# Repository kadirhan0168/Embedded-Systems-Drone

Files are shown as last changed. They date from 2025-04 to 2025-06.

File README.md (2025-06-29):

# Embedded Systems Drone

## Description

This project implements a WiFi-controlled drone using ESP32 microcontroller with MPU6050 accelerometer/gyroscope for stabilization. The drone can be controlled via a web interface that displays real-time orientation data and allows adjustment of PID parameters.

**Want to understand how it works internally?**  
See the [Project Overview Document](docs/overview.md) for full system architecture, hardware schematics, software design, flowcharts, API docs, and more.

### Features

The system has the following features:

- PID control for drone stabilization
- Web-based controller dashboard
- UDP communication for emergency stop and telemetry
- Power-saving sleep mode
- Watchdog timer for system reliability

## Prerequisites

### Hardware

#### Drone:
- ESP32CAM development board
- ESP32-CAM-MB micro USB programmer
- Jumper wires
- MPU6050 6-axis accelerometer/gyroscope
- 4x 8520 brushed motors
- 4x MOSFET-based motor drivers
- 2x LiPo batteries
- WiFi network
- Drone frame STL files

#### Telemetry & Emergency Stop Controller:
- ESP32 development board
- 16x2 I2C LCD
- Button
- 10kΩ resistor

### Software

- ESP-IDF
- Arduino Core for ESP32
- Required libraries:
  - `MPU6050` (I2C communication)
  - `WiFi`
  - `ESPAsyncWebServer`
  - `WiFiUdp`

## Get Started

1. Clone this repository:
   ```bash
   git clone https://github.com/kadirhan0168/Embedded-Systems-Drone.git
   ```
2. Set up ESP-IDF development environment.
3. Add Arduino as a component to your project.
4. Configure the project:

   ```bash
   idf.py menuconfig
   ```

## Setup

### Drone:

1. Build the drone.
2. Wire all components according to `docs/schematics/embedded-systems-drone.pdf`.
3. Adjust WiFi credentials in `main/main.cpp`.
4. Connect ESP32-CAM-MB micro USB programmer to the onboard ESP32CAM module through jumper wires. Make sure to also connect IO0 to GND when flashing.
5. Set correct serial port.
6. Build and flash the project using UART.
7. Open the serial monitor to find the controller dashboard IP.

### Telemetry & Emergency Stop Controller:

1. Build the Telemetry & Emergency Stop Controller according to `docs/schematics/embedded-systems-telemetry-controller.pdf`.
2. Power the ESP32 through USB.

## Usage

The drone will initialize its system and connect to WiFi when powered on. Connect to the controller dashboard by accessing the drone's IP address (acquired from serial monitor) in a web browser. 

The power slider increases the power output of the motors. The power value is the PWM signal with 0 being the lowest and 255 being the highest power output. The directional buttons move the drone along the X- and Y-axes through roll & pitch movements. The rotation controls handle the yaw movements to rotate the drone along the Z-axis.

The PID terms can be adjusted through the controller dahsboard using the `Kp`, `Ki`, and `Kd` fields. :warning:**Attention**:warning: — The PID terms **are not** saved, they will get lost if the connection to the drone disconnects. Save the PID terms manually if they are of importance.

The Telemetry & Emergency Stop Controller will initialize its system and attempt connecting to the drone's access point when powered on. It will display the drone's pitch and roll values on the LCD when the connection has been set up. Pressing the button will trigger an interrupt cutting all power to the drone's motors immediately.

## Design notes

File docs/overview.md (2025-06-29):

# Project Overview: Embedded Systems Drone

This document provides a high-level overview of the system design and architecture for the Embedded Systems Drone project. It links to all major documentation files, including hardware schematics, software architecture, 3D designs, API documentation, and test reports.

---

## 1. Hardware Design

### 1.1 Drone Hardware

- [Drone Circuit Schematics (PDF)](schematics/embedded-systems-drone.pdf)
  
  Wiring diagram for the drone's components, including the ESP32-CAM, MPU6050 IMU, motor drivers, and power supply.

- [Drone Frame STL File (V3)](designs/V3/drone.stl)
  
  3D-printable STL models of the drone's frame designed for an X-configuration with four arms:
  - V1 was designed for use with 716 motors.
  - V2 was designed for use with 8520 motors.
  - V3 is a bigger frame whic was also designed for use with 8520 motors.

### 1.2 Telemetry & Emergency Stop Controller

- [Controller Circuit Schematics (PDF)](schematics/embedded-systems-telemetry-controller.pdf)

  Full schematic for the telemetry controller, including button wiring, I²C LCD, and UDP communication to the drone.

### 1.3 Hardware Architecture

- [System Architecture Diagram](diagrams/architecture-design-embedded-systems.png)
  
  High-level component diagram showing the hardware and subsystem layout of both the drone and the telemetry controller. Arrows represent interaction and data flow between physical components and modules.

---

## 2. Software Design

### 2.1 Software Architecture
- [Data Flow Diagram](diagrams/dataflow-embedded-systems.png)

  Diagram outlining how data moves between components in the system, such as I²C, UDP, PWM.

### 2.2 Flowcharts

- [Drone Flowchart](diagrams/flowchart-drone-embedded-systems.png)

  Step-by-step control logic of the drone’s firmware, including tasks like PID control, WiFi, telemetry broadcast, UDP listener.

- [Telemetry Controller Flowchart](diagrams/flowchart-telemetry-embedded-systems.png)

  Logical flow of the telemetry controller from setup to emergency stop trigger and telemetry display.

### 2.3 HTTP API

- [HTTP Endpoint Documentation](HTTP/HTTP_API.md)

  Full list and explanation of HTTP endpoints exposed by the drone’s web server, including `/setMotorPower`, `/getMPUData`, and `/setPID`.

---

## 3. Test Reports

- [Test Reports](test-reports/drone-test-reports.md)

  Results from testing the drone's core features.

---

## Related Code Files

| Module | Location |
|---|---|
| Drone Firmware | `firmware/drone/main/main.cpp` |
| Telemetry Controller Code | `firmware/telemetry_controller/drone_telemetry_controller.ino` |

---

## 🔗 Quick Links

- [Project README](../README.md)
- [Setup Instructions](../README.md#get-started)

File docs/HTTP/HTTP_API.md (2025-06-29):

# Drone Web Server API Endpoints

## General Control

| Endpoint | Method | Parameters | Description | Example Response (JSON) |
|---|---|---|---|---|
| `/setMotorPower` | GET | `value` (0–255) | Sets the motor power. Wakes up drone if sleeping. | `{"status":"OK","pitch":1.2,"roll":-0.5}` |
| `/getMPUData` | GET | — | Returns current pitch and roll values. | `{"pitch":0.0,"roll":1.8}` |
| `/getSleepStatus`| GET | — | Returns whether the drone is currently sleeping. | `{"isSleeping":false}` |

---

## Movement Commands

| Endpoint | Method | Parameters | Description | Response |
|---|---|---|---|---|
| `/moveForward`  | GET | — | Move drone forward | `"Moving Up"` |
| `/moveBackward` | GET | — | Move drone backward | `"Moving Down"` |
| `/moveLeft` | GET | — | Move drone to the left | `"Moving Left"` |
| `/moveRight` | GET | — | Move drone to the right | `"Moving Right"` |
| `/rotateLeft` | GET | — | Rotate drone counter-clockwise | `"Rotating Left"` |
| `/rotateRight`  | GET | — | Rotate drone clockwise | `"Rotating Right"` |
| `/stop` | GET | — | Stops all directional movement | `"Stopping Movement"` |

---

## PID Tuning

| Endpoint | Method | Parameters | Description | Example Response |
|---|---|---|---|---|
| `/setPID` | GET | `Kp`, `Ki`, `Kd` (floats) | Updates the PID controller constants| `"PID Updated: Kp=2.0 Ki=0.01 Kd=0.5"` |

| Endpoint  | Method | Parameters (floats)  | Description | Defaults | Example Response |
|---|---|---|---|---|---|
| `/setPID` | GET | `Kp`, `Ki`, `Kd` | Updates the PID controller constants | `Kp=1.5` | `"PID Updated: Kp=2.0 Ki=0.01 Kd=0.5"` |
| | | | | `Ki=0.003` | |
| | | | | `Kd=0.0` | |

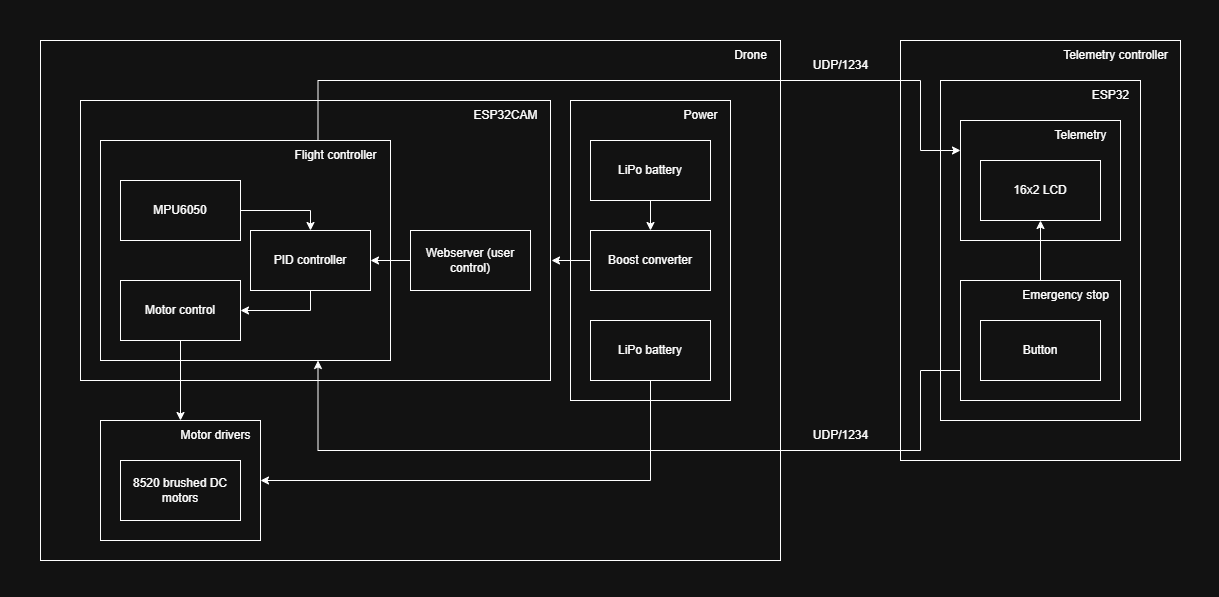
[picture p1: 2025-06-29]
docs/diagrams/architecture-design-embedded-systems.png

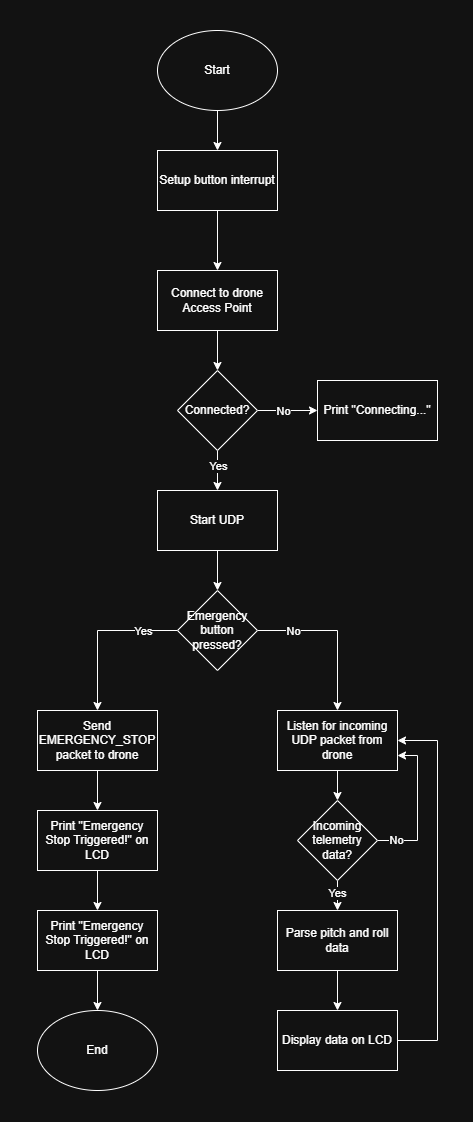
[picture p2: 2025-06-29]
docs/diagrams/flowchart-telemetry-embedded-systems.png

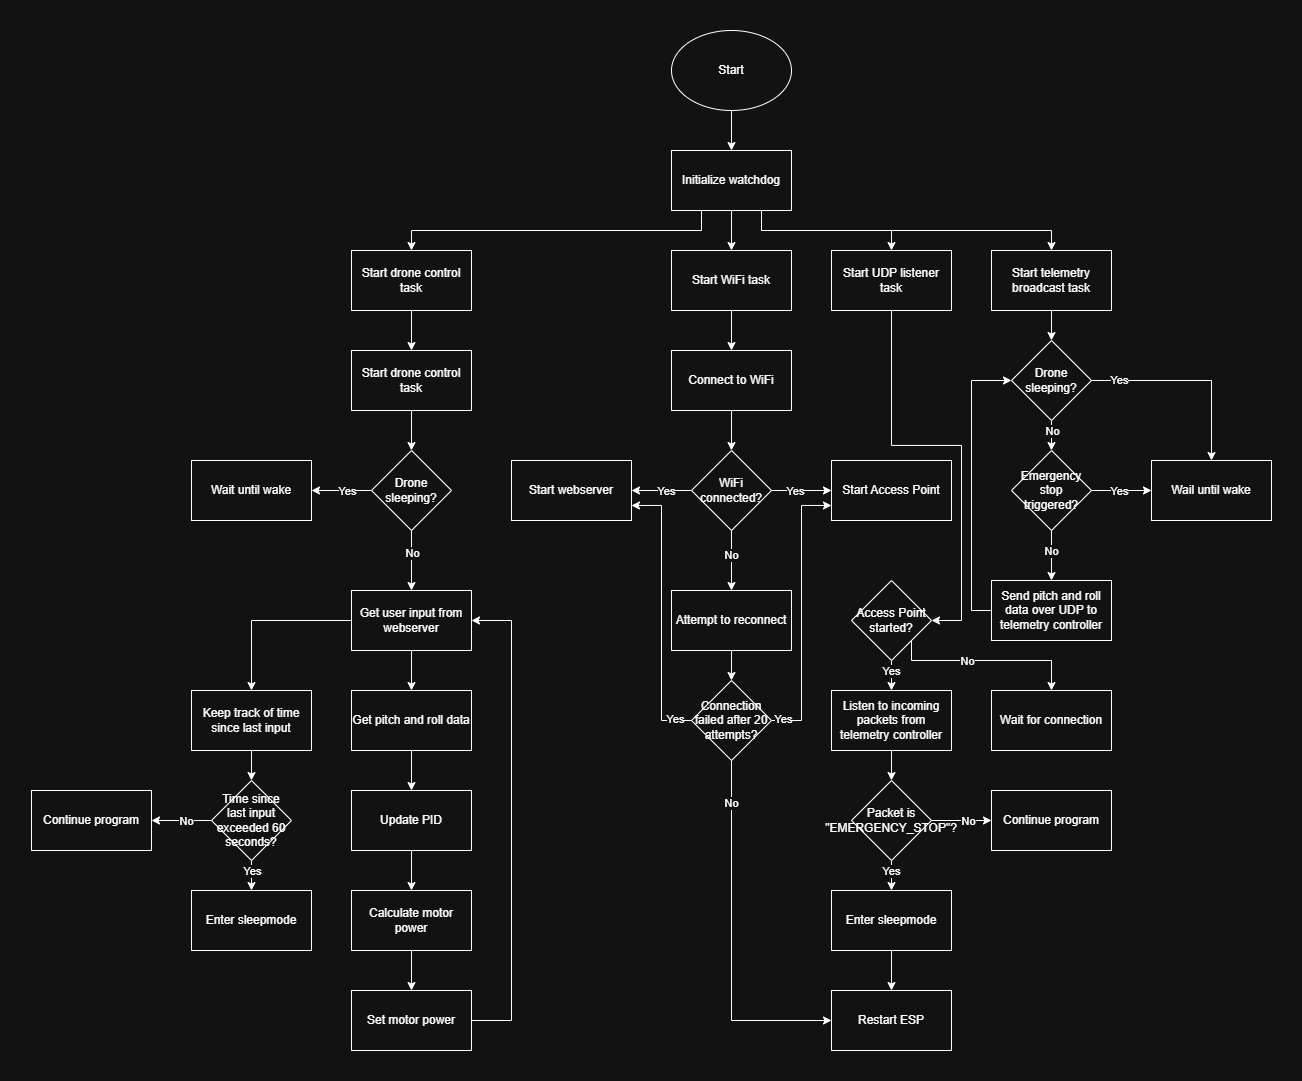
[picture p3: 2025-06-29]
docs/diagrams/flowchart-drone-embedded-systems.png

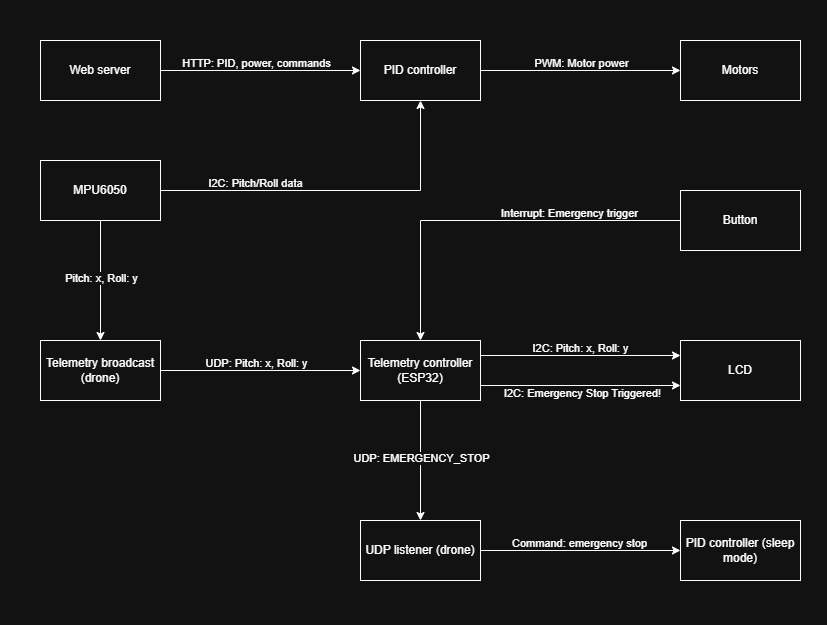
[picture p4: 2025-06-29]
docs/diagrams/dataflow-embedded-systems.png

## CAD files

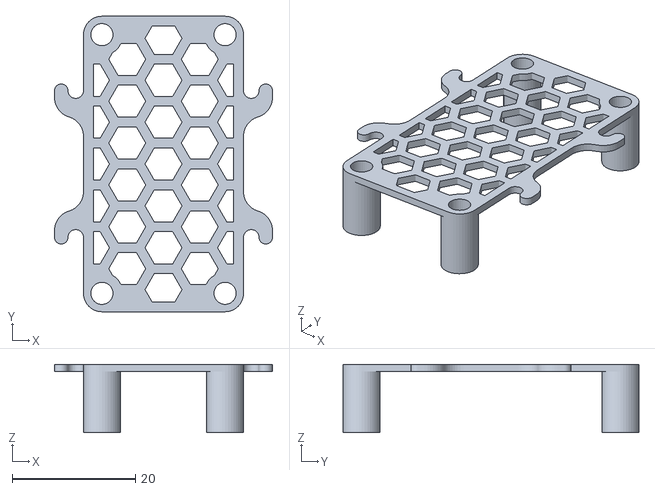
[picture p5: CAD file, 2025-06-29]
docs/designs/V3/Batteryholder.stl
35.4 x 48.0 x 11.1

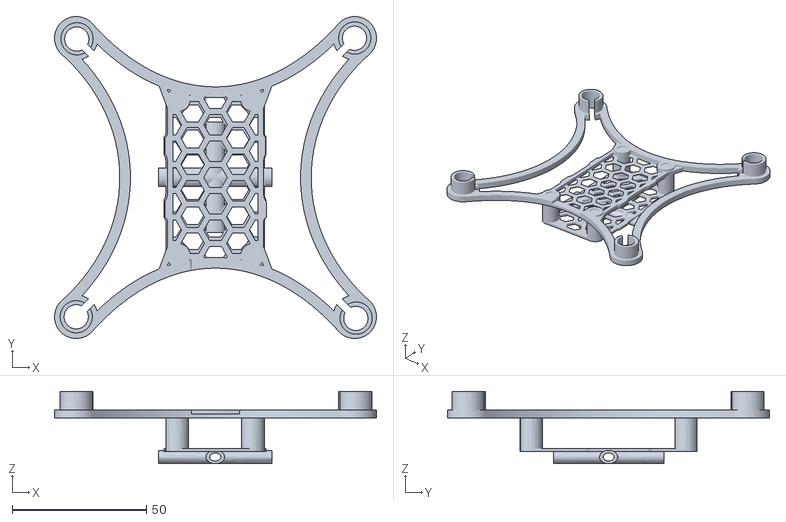
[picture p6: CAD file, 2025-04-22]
docs/designs/V3/Drone.stl
120.0 x 120.0 x 27.0

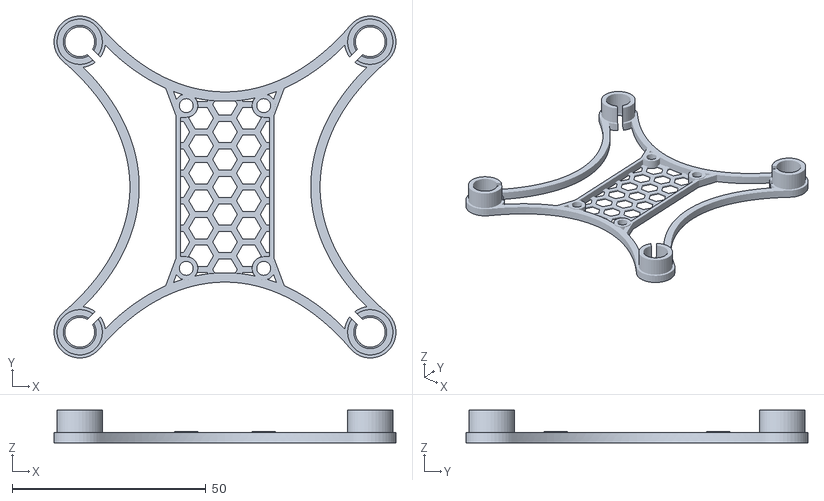
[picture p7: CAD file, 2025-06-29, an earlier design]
docs/designs/V2/micro105-bottom-v2.stl
88.3 x 88.3 x 8.50

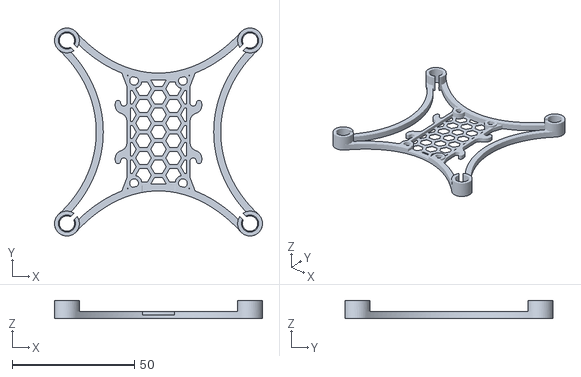
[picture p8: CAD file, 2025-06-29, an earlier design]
docs/designs/V1/micro105-bottom-v4-7mm-bottom-battery.stl
85.2 x 85.2 x 7.50

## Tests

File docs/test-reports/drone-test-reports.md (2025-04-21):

# Test report - ESP32 drone functionalities

## Test 1: Hosting webserver as controller dashboard

### Context

This test verifies that the ESP32CAM module is able to connect to WiFi and host a webserver. The webserver contains the HTML for the controller dashboard.

### Requirement

Hosting webserver for controls.

### Acceptance criteria

The ESP32CAM connects to WiFi and hosts the webserver correctly.

### Materials needed

- ESP32CAM
- ESP32-CAM-MB micro USB programmer
- WiFi network
- main.cpp

### Preparation

1. Clone the repository.
2. Connect the ESP32-CAM-MB micro USB programmer to the ESP32CAM module.
3. Select the correct serial port.
4. Build and flash main.cpp.

### Execution

1. Open serial monitor and wait for the IP address to be printed.
2. Connect to the IP address through the browser.

### Results

The browser connected to the webserver and the correct HTML page was being hosted.

### Conclusion

The test passed. The ESP32CAM module was able to connect to WiFi and host the webserver.

----

## Test 2: Throttle

### Context

This test verifies that the drone is able to increase and decrease thrust to all motors using the controller dashboard.

### Requirement  

Ascend
Descend

### Acceptance criteria

Changing the PWM signal using the controllers dashboard's slider should increase or decrease motor power output accordingly.

### Materials needed 

- Fully built drone
- Jumper wires
- ESP32-CAM-MB micro USB programmer
- WiFi network
- main.cpp
- 2x LiPo batteries

### Preparation

1. Clone the repository.
2. Connect the ESP32-CAM-MB micro USB programmer to the ESP32CAM module.
3. Change the WiFi credentials in main.cpp
4. Select the correct serial port.
5. Build and flash main.cpp.
6. Connect LiPo batteries to the drone.

### Execution

1. Open serial monitor and wait for the IP address to be printed.
2. Connect to the IP address through the browser.
3. Adjust the throttle using the slider.
4. Observe whether the drone's motors spin faster as the throttle increases, and slower as it decreases.

### Results

The drone's motors spin faster as the throttle increases. The motors spin slower when the throttle decreases and come to a full stop at a PWM signal of 0.

### Conclusion

The test passed. The motors responded accordingly to the throttle inputs.

----

## Test 3: Pitch & roll in all directions

### Context

This test verifies the movement of the drone along the X- and Y-axes.

### Requirement  

Pitch in four directions.

### Acceptance criteria

The test passes if the drone is able to pitch forward, backward, and roll to the sides to move in all four directions. It also tests wether the motors are configured correctly.

### Materials needed 

- Fully built drone
- Jumper wires
- ESP32-CAM-MB micro USB programmer
- WiFi network
- main.cpp
- 2x LiPo batteries

### Preparation

1. Clone the repository.
2. Connect the ESP32-CAM-MB micro USB programmer to the ESP32CAM module.
3. Change the WiFi credentials in main.cpp
4. Select the correct serial port.
5. Build and flash main.cpp.
6. Connect LiPo batteries to the drone.

### Execution

1. Open serial monitor and wait for the IP address to be printed.
2. Connect to the IP address through the browser.
3. Increase the throttle using the slider while holding the drone at a level where you can feel it starting to lift.
4. Press each of the four directional buttons individually and feel which way the drone wants to move.

### Results

Pressing the directional buttons made the drone want to move in the correct direction. The thrust was high enough to see the drone pulling into each direction.

### Conclusion

The test passed. The drone is able to pitch and roll accordingly based on user inputs. This also verifies that the motors are configured correctly.

----

## Test 4: Yaw left and right

### Context

This test verifies the rotational movement of the drone along the Z-axis (yaw).

### Requirement  

Yaw left and right.

### Acceptance criteria

The test passes if the drone is able to rotate clockwise and counterclockwise when the respective yaw buttons are pressed.

### Materials needed 

- Fully built drone
- Jumper wires
- ESP32-CAM-MB micro USB programmer
- WiFi network
- main.cpp
- 2x LiPo batteries

### Preparation

1. Clone the repository.
2. Connect the ESP32-CAM-MB micro USB programmer to the ESP32CAM module.
3. Change the WiFi credentials in main.cpp
4. Select the correct serial port.
5. Build and flash main.cpp.
6. Connect LiPo batteries to the drone.

### Execution

1. Open serial monitor and wait for the IP address to be printed.
2. Connect to the IP address through the browser.
3. Increase the throttle using the slider while holding the drone at a level where you can feel it starting to lift.
4. Press each of the two yaw buttons individually and feel which way the drone wants to move.

### Results

Pressing the yaw buttons made the drone want to move in the correct direction.

### Conclusion

The test passed. The drone is able to rotate along the Z-axis in both directions.

## Test 5: Reading the MPU6050 sensor via I2C

### Context
This test verifies whether the ESP32CAM can read data from the MPU6050 sensor via I2C communication.

### Requirement
The ESP32CAM must be able to read data from a connected MPU6050 sensor via I2C.

### Acceptance criteria
The sensor must return correct acceleration and gyroscopic data.

### Materials needed
- ESP32CAM
- ESP32-CAM-MB micro USB programmer
- MPU6050
- Jumper wires
- main.cpp

### Preparation
1. Connect the MPU6050 to the ESP32CAM module using jumper wires.
2. Select the correct serial port.
3. Build and flash main.cpp.

### Execution

1. Open the serial monitor.
2. Move the MPU6050 around and check whether the incoming data is correct and reliable. The stream of data should be stable and uninterrupted.

### Conclusion
The test passed. The MPU6050 readout works as expected. The data is reliable, and communication is stable. The test passed successfully.

----

## Test 6: Balance drone using MPU6050

### Context

This test verifies the balancing of the drone using the MPU6050 module and PID controller.

### Requirement  

Balance drone using gyroscope.

### Acceptance criteria

The test passes if the drone is able to ascend, maintain altitude and balance itself without drifting away more than 10 centimeters from it's initial position during 30 seconds of flight.

### Materials needed 

- Fully built drone
- Jumper wires
- ESP32-CAM-MB micro USB programmer
- WiFi network
- main.cpp
- 2x LiPo batteries
- Duct tape
- Stopwatch

### Preparation

1. Clone the repository.
2. Connect the ESP32-CAM-MB micro USB programmer to the ESP32CAM module.
3. Change the WiFi credentials in main.cpp
4. Select the correct serial port.
5. Build and flash main.cpp.
6. Connect LiPo batteries to the drone.
7. Stick a piece of duct tape to the floor and place the drone on top of it.

### Execution

1. Open serial monitor and wait for the IP address to be printed.
2. Connect to the IP address through the browser.
3. Increase the throttle using the slider until the drone starts ascending and is approximately 50 centimeters above the floor.
4. Start the stopwatch and observer the drone.

### Results

The drone struggles to maintain balance and altitude. It loses balance and crashes shortly after ascending.

### Conclusion

The test failed. The drone tries to stabilize too aggressively is not able to maintain flight. The PID controller needs further calibration.

----

## Test 7: Watchdog timer

### Context
This test verifies whether the watchdog timer in the ESP32 microcontroller functions correctly by detecting system faults and restarting the drone.

### Requirement
The ESP32 must use a watchdog timer that automatically restarts the system in case of errors.

### Acceptance criteria
The watchdog must restart the drone within 3 seconds after detecting a system error or freeze.

### Materials needed
- Fully built drone
- ESP32-CAM-MB micro USB programmer
- Jumper wires
- main.cpp

### Execution
1. Open the serial monitor.
2. Observe whether the watchdog timer gets triggered.

### Results
The watchdog timer functioned correctly. The drone restarted within the expected time after detecting a system error. No communication issues were observed during the test.

### Conclusion
The watchdog timer test was successful. The function works as required and restarts the drone within the specified time.

----

## Test 8: Sleep mode

### Context
This test checks the functionality of the sleep mode on the ESP32, which helps save energy during inactivity.

### Requirement
The ESP32 must automatically enter sleep mode during inactivity to conserve energy.

### Acceptance criteria
The drone must enter sleep mode within a minute of inactivity and correctly wake up upon receiving an input signal.

### Materials needed
- Fully built drone
- ESP32-CAM-MB micro USB programmer
- Jumper wires
- main.cpp
- WiFi network
- Stopwatch

### Execution
1. Open serial monitor and wait for the IP address to be printed.
2. Connect to the IP address through the browser.
3. Start the stopwatch and wait for the drone to go into sleep mode.

### Results
The sleep mode functioned as expected. The drone entered sleep mode after a minute of inactivity and was reactivated immediately after a trigger. A message was displayed on the controller dashboard to notify the user that the drone was in sleep mode. The MPU6050 was also powered off during this state.

### Conclusion
Sleep mode is effective, and the drone wakes correctly upon receiving input. The test passed successfully.

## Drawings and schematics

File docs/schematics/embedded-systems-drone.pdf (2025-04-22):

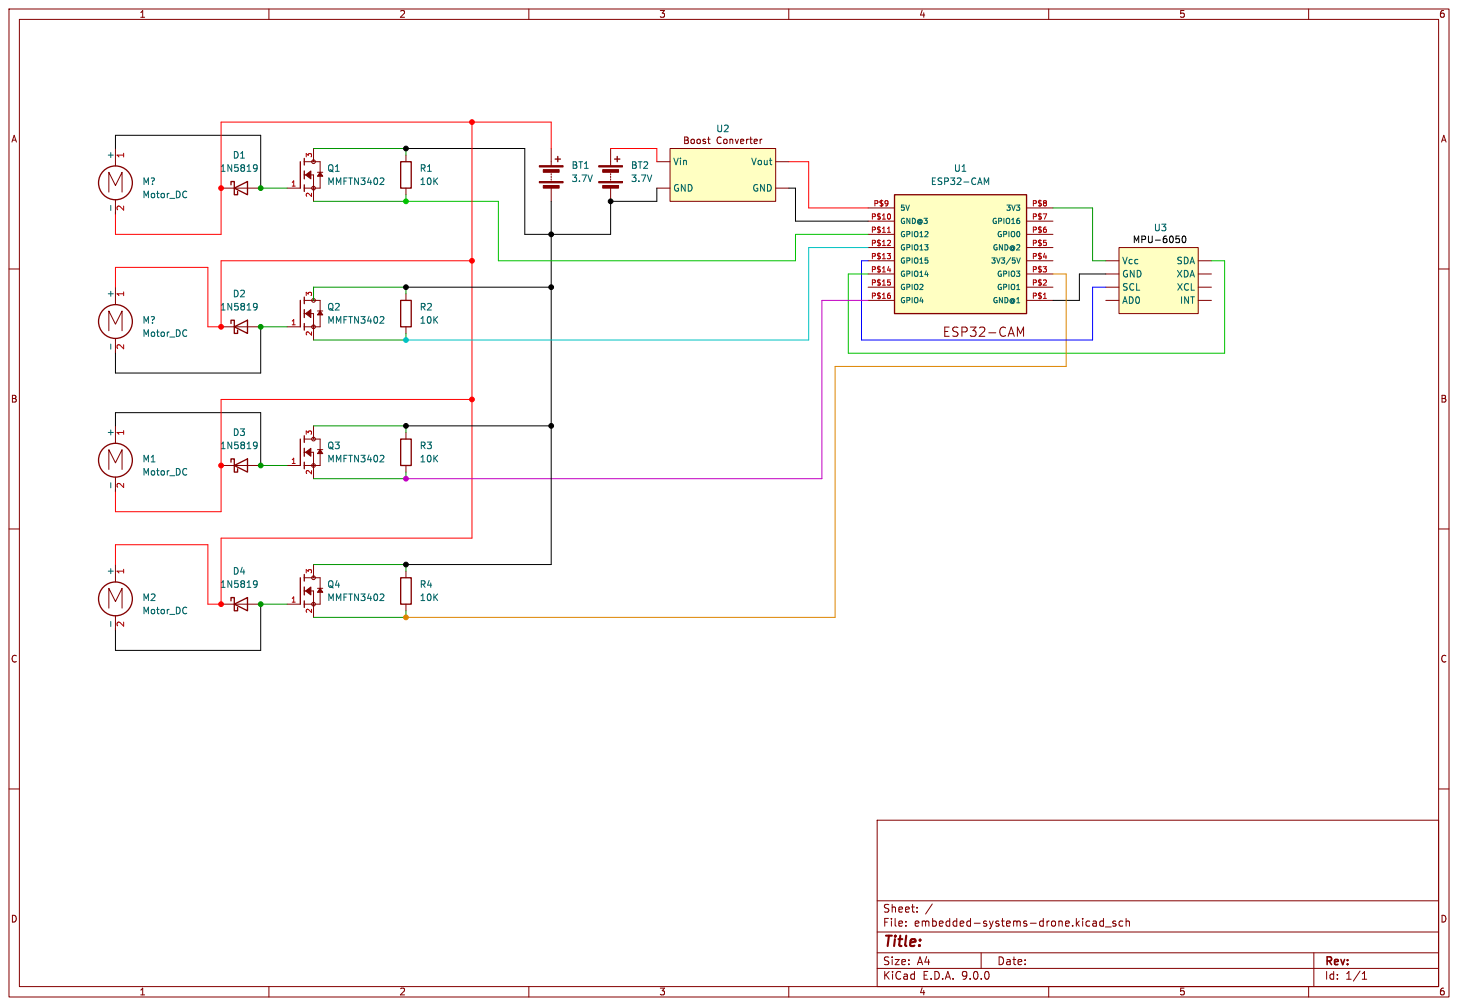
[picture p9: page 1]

Boost Converter Vin GND

Id: 1/1 Title: File: embedded-systems-drone.kicad_sch Sheet: /

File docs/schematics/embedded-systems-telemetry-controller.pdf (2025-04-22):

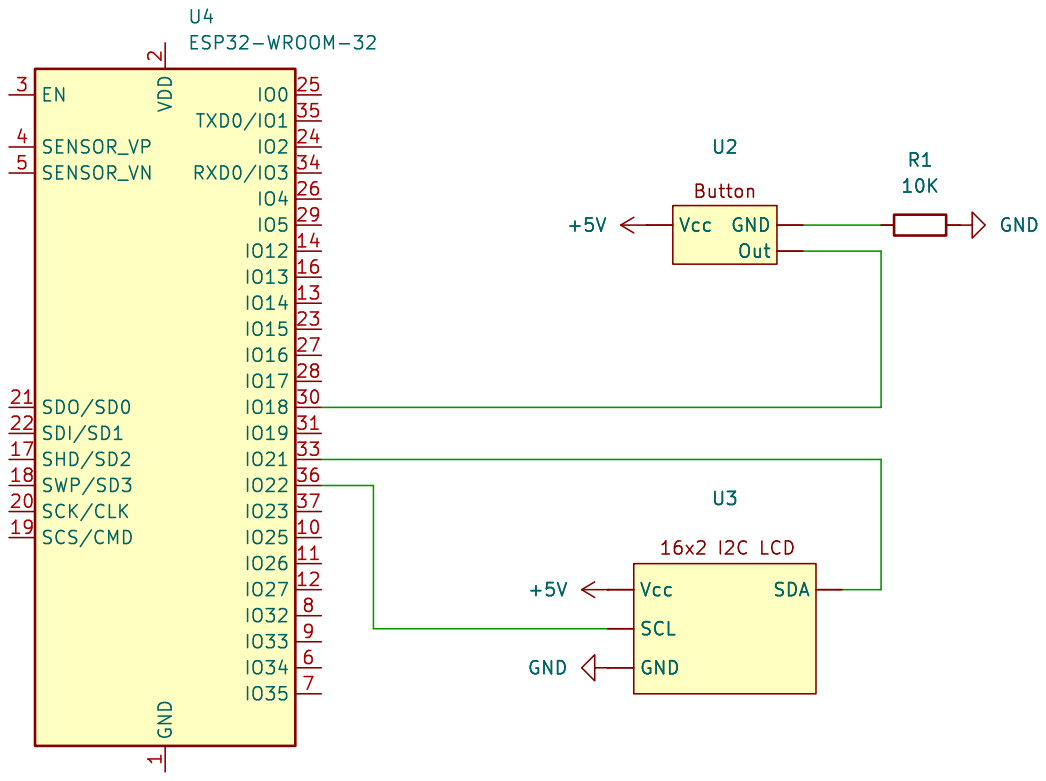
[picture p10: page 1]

Id: 1/1 Title: File: embedded-systems-telemetry-controller.kicad_sch Sheet: /

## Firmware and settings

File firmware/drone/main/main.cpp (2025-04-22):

#include <stdio.h>
#include <string.h>
#include "esp_system.h"
#include "esp_log.h"
#include "nvs_flash.h"
#include "freertos/FreeRTOS.h"
#include "freertos/task.h"
#include "mpu6050.h"
#include <driver/i2c.h>
#include "driver/ledc.h"
#include <math.h>
#include <Arduino.h>
#include <WiFi.h>
#include <ESPAsyncWebServer.h>
#include <WiFiUdp.h>
#include "esp_task_wdt.h"

#define SSID "ssid"
#define PASSWORD "password"

AsyncWebServer server(80);

#define M_PI 3.14159265358979323846

#define PIN_SDA 14
#define PIN_CLK 15
#define I2C_ADDRESS 0x68

#define MPU6050_ACCEL_XOUT_H 0x3B
#define MPU6050_PWR_MGMT_1   0x6B

#undef ESP_ERROR_CHECK
#define ESP_ERROR_CHECK(x)   do { esp_err_t rc = (x); if (rc != ESP_OK) { ESP_LOGE("err", "esp_err_t = %d", rc); assert(0 && #x);} } while(0);

// PWM definitions
#define LEDC_TIMER LEDC_TIMER_0
#define LEDC_MODE LEDC_LOW_SPEED_MODE
#define LEDC_DUTY_RES LEDC_TIMER_8_BIT
#define LEDC_FREQUENCY 4000

// MPU6050 definitions
#define I2C_MASTER_NUM I2C_NUM_0
#define I2C_MASTER_FREQ_HZ 100000
#define I2C_MASTER_SDA_IO 14
#define I2C_MASTER_SCL_IO 15
#define MPU6050_ADDR 0x68

// Motor pins
int motorPin[4] = {
    4, 
    3, 
    13, 
    12
};

// UDP configuration
WiFiUDP udp;
const unsigned int localPort = 1234;
const unsigned int remotePort = 1234;
IPAddress broadcastIP(192, 168, 4, 255);
TaskHandle_t udpTaskHandle = NULL;

// Emergency stop variables
volatile bool emergency_stop = false;
portMUX_TYPE emergency_mux = portMUX_INITIALIZER_UNLOCKED;

// Pet every 500ms
const int WDT_TIMEOUT_SEC = 5;
const int PET_INTERVAL_MS = 500;

static char mpuTag[] = "mpu6050";
static char droneTag[] = "droneControl";
static char emergencyTag[] = "emergencyController";

float pitch = 0.0;
float roll = 0.0;
float targetPitch = 0.0;
float targetRoll = 0.0;

float Kp = 1.5;
float Ki = 0.003; 
float Kd = 0.0;

float pitchError = 0.0;
float rollError = 0.0;
float pitchIntegral = 0.0;
float rollIntegral = 0.0;
float previousPitchError = 0.0;
float previousRollError = 0.0;
float pitchCorrection = 0.0;
float rollCorrection = 0.0;

int motorPower = 0;

bool isSleeping = false;
uint64_t lastActivityTime = 0;
const uint64_t sleepTimeout = 60000;

// I2C initialization
static esp_err_t i2c_master_init(void) {
    i2c_config_t conf;
    conf.mode = I2C_MODE_MASTER;
    conf.sda_io_num = I2C_MASTER_SDA_IO;
    conf.scl_io_num = I2C_MASTER_SCL_IO;
    conf.sda_pullup_en = GPIO_PULLUP_ENABLE;
    conf.scl_pullup_en = GPIO_PULLUP_ENABLE;
    conf.master.clk_speed = I2C_MASTER_FREQ_HZ;

    esp_err_t err = i2c_param_config(I2C_MASTER_NUM, &conf);
    if (err != ESP_OK) {
        return err;
    }

    return i2c_driver_install(I2C_MASTER_NUM, conf.mode, 0, 0, 0);
}

// MPU6050 initialization
void setupMPU() {
    esp_err_t ret = i2c_master_init();
    if (ret != ESP_OK) {
        ESP_LOGE(mpuTag, "I2C initialization failed: %s", esp_err_to_name(ret));
        return;
    }

    // Wake up MPU6050
    uint8_t data[2] = {0x6B, 0x00}; // PWR_MGMT_1 register
    ret = i2c_master_write_to_device(I2C_MASTER_NUM, MPU6050_ADDR, data, sizeof(data), pdMS_TO_TICKS(1000));
    
    if (ret == ESP_OK) {
        ESP_LOGI(mpuTag, "MPU6050 connected and initialized");
    } else {
        ESP_LOGE(mpuTag, "MPU6050 connection failed: %s", esp_err_to_name(ret));
        esp_restart();
    }
}

// Read MPU6050 data
void readMPU() {
    uint8_t accel_data[6];
    uint8_t gyro_data[6];
    
    // Read accelerometer data
    uint8_t reg_addr = 0x3B; // ACCEL_XOUT_H register
    esp_err_t ret = i2c_master_write_read_device(I2C_MASTER_NUM, MPU6050_ADDR, 
                                               &reg_addr, 1, accel_data, 6, pdMS_TO_TICKS(1000));
    
    if (ret != ESP_OK) {
        ESP_LOGE(mpuTag, "Failed to read accelerometer data: %s", esp_err_to_name(ret));
        return;
    }
    
    if (ret != ESP_OK) {
        ESP_LOGE(mpuTag, "Failed to read gyroscope data: %s", esp_err_to_name(ret));
        return;
    }
    
    int16_t ax = (accel_data[0] << 8) | accel_data[1];
    int16_t ay = (accel_data[2] << 8) | accel_data[3];
    int16_t az = (accel_data[4] << 8) | accel_data[5];

    // Calculate pitch and roll
    pitch = atan2(ay, sqrt(ax * ax + az * az)) * 180.0 / M_PI;
    roll = atan2(-ax, az) * 180.0 / M_PI;
}

// PID controller update
void updatePID() {
    if (motorPower <= 0) {
        pitchIntegral = 0;
        rollIntegral = 0;
        return;
    }

    pitchError = targetPitch - pitch;
    rollError = targetRoll - roll;
    
    ESP_LOGD(mpuTag, "Pitch: %.2f | Roll: %.2f | Pitch Error: %.2f | Roll Error: %.2f", 
             pitch, roll, pitchError, rollError);

    pitchIntegral += pitchError;
    rollIntegral += rollError;

    float pitchDerivative = pitchError - previousPitchError;
    float rollDerivative = rollError - previousRollError;

    pitchCorrection = Kp * pitchError + Ki * pitchIntegral + Kd * pitchDerivative;
    rollCorrection = Kp * rollError + Ki * rollIntegral + Kd * rollDerivative;

    previousPitchError = pitchError;
    previousRollError = rollError;
}

ledc_channel_t led_channels[4] = {
    LEDC_CHANNEL_0, 
    LEDC_CHANNEL_1, 
    LEDC_CHANNEL_2, 
    LEDC_CHANNEL_3
};

// Motor PWM setup
void setupMotors() {
    ledc_timer_config_t ledc_timer = {
        .speed_mode = LEDC_LOW_SPEED_MODE,
        .duty_resolution = LEDC_TIMER_8_BIT,
        .timer_num = LEDC_TIMER_0,
        .freq_hz = 5000,
        .clk_cfg = LEDC_AUTO_CLK
    };
    ESP_ERROR_CHECK(ledc_timer_config(&ledc_timer));

    for (int i = 0; i < 4; i++) {
        ledc_channel_config_t ledc_channel = {
            .gpio_num    = motorPin[i],
            .speed_mode  = LEDC_LOW_SPEED_MODE,
            .channel     = led_channels[i],
            .intr_type   = LEDC_INTR_DISABLE,
            .timer_sel   = LEDC_TIMER_0,
            .duty        = 0,
            .hpoint      = 0
        };
        ESP_ERROR_CHECK(ledc_channel_config(&ledc_channel));
    }
}

// Stabilize drone
void stabilizeDrone() {
    float motor1Power, motor2Power, motor3Power, motor4Power;
    
    if (motorPower <= 0) {
        motor1Power = motor2Power = motor3Power = motor4Power = 0;
    } else if (motorPower <= 10) {
        motor1Power = motor2Power = motor3Power = motor4Power = motorPower;
    } else {
        motor1Power = motorPower + pitchCorrection + rollCorrection;
        motor2Power = motorPower + pitchCorrection - rollCorrection;
        motor3Power = motorPower - pitchCorrection - rollCorrection;
        motor4Power = motorPower - pitchCorrection + rollCorrection;
    }

    // Constrain motor power values
    motor1Power = constrain(motor1Power, 0, 255);
    motor2Power = constrain(motor2Power, 0, 255);
    motor3Power = constrain(motor3Power, 0, 255);
    motor4Power = constrain(motor4Power, 0, 255);

    ESP_LOGD(droneTag, "Motor Powers: %.1f | %.1f | %.1f | %.1f", 
             motor1Power, motor2Power, motor3Power, motor4Power);

    // Write PWM to motors
    ESP_ERROR_CHECK(ledc_set_duty(LEDC_MODE, LEDC_CHANNEL_0, (uint32_t)motor1Power));
    ESP_ERROR_CHECK(ledc_update_duty(LEDC_MODE, LEDC_CHANNEL_0));
    
    ESP_ERROR_CHECK(ledc_set_duty(LEDC_MODE, LEDC_CHANNEL_1, (uint32_t)motor2Power));
    ESP_ERROR_CHECK(ledc_update_duty(LEDC_MODE, LEDC_CHANNEL_1));
    
    ESP_ERROR_CHECK(ledc_set_duty(LEDC_MODE, LEDC_CHANNEL_2, (uint32_t)motor3Power));
    ESP_ERROR_CHECK(ledc_update_duty(LEDC_MODE, LEDC_CHANNEL_2));
    
    ESP_ERROR_CHECK(ledc_set_duty(LEDC_MODE, LEDC_CHANNEL_3, (uint32_t)motor4Power));
    ESP_ERROR_CHECK(ledc_update_duty(LEDC_MODE, LEDC_CHANNEL_3));
}

// Movement functions
void moveForward() {
    ESP_LOGI(droneTag, "Moving Forward");
    ESP_ERROR_CHECK(ledc_set_duty(LEDC_MODE, LEDC_CHANNEL_0, motorPower));
    ESP_ERROR_CHECK(ledc_set_duty(LEDC_MODE, LEDC_CHANNEL_1, motorPower / 2));
    ESP_ERROR_CHECK(ledc_set_duty(LEDC_MODE, LEDC_CHANNEL_2, motorPower));
    ESP_ERROR_CHECK(ledc_set_duty(LEDC_MODE, LEDC_CHANNEL_3, motorPower / 2));
    
    // Update duty cycles
    for (int i = 0; i < 4; i++) {
        ESP_ERROR_CHECK(ledc_update_duty(LEDC_MODE, led_channels[i]));
    }
}

void moveBackward() {
    ESP_LOGI(droneTag, "Moving Backward");
    ESP_ERROR_CHECK(ledc_set_duty(LEDC_MODE, LEDC_CHANNEL_0, motorPower / 2));
    ESP_ERROR_CHECK(ledc_set_duty(LEDC_MODE, LEDC_CHANNEL_1, motorPower));
    ESP_ERROR_CHECK(ledc_set_duty(LEDC_MODE, LEDC_CHANNEL_2, motorPower / 2));
    ESP_ERROR_CHECK(ledc_set_duty(LEDC_MODE, LEDC_CHANNEL_3, motorPower));
    
    for (int i = 0; i < 4; i++) {
        ESP_ERROR_CHECK(ledc_update_duty(LEDC_MODE, led_channels[i]));
    }
}

void moveLeft() {
    ESP_LOGI(droneTag, "Moving Left");
    ESP_ERROR_CHECK(ledc_set_duty(LEDC_MODE, LEDC_CHANNEL_0, motorPower));
    ESP_ERROR_CHECK(ledc_set_duty(LEDC_MODE, LEDC_CHANNEL_1, motorPower));
    ESP_ERROR_CHECK(ledc_set_duty(LEDC_MODE, LEDC_CHANNEL_2, motorPower / 2));
    ESP_ERROR_CHECK(ledc_set_duty(LEDC_MODE, LEDC_CHANNEL_3, motorPower / 2));
    
    for (int i = 0; i < 4; i++) {
        ESP_ERROR_CHECK(ledc_update_duty(LEDC_MODE, led_channels[i]));
    }
}

void moveRight() {
    ESP_LOGI(droneTag, "Moving Right");
    ESP_ERROR_CHECK(ledc_set_duty(LEDC_MODE, LEDC_CHANNEL_0, motorPower / 2));
    ESP_ERROR_CHECK(ledc_set_duty(LEDC_MODE, LEDC_CHANNEL_1, motorPower / 2));
    ESP_ERROR_CHECK(ledc_set_duty(LEDC_MODE, LEDC_CHANNEL_2, motorPower));
    ESP_ERROR_CHECK(ledc_set_duty(LEDC_MODE, LEDC_CHANNEL_3, motorPower));
    
    for (int i = 0; i < 4; i++) {
        ESP_ERROR_CHECK(ledc_update_duty(LEDC_MODE, led_channels[i]));
    }
}

void rotateLeft() {
    ESP_LOGI(droneTag, "Rotating Left");
    ESP_ERROR_CHECK(ledc_set_duty(LEDC_MODE, LEDC_CHANNEL_0, motorPower));
    ESP_ERROR_CHECK(ledc_set_duty(LEDC_MODE, LEDC_CHANNEL_1, motorPower / 2));
    ESP_ERROR_CHECK(ledc_set_duty(LEDC_MODE, LEDC_CHANNEL_2, motorPower / 2));
    ESP_ERROR_CHECK(ledc_set_duty(LEDC_MODE, LEDC_CHANNEL_3, motorPower));
    
    for (int i = 0; i < 4; i++) {
        ESP_ERROR_CHECK(ledc_update_duty(LEDC_MODE, led_channels[i]));
    }
}

void rotateRight() {
    ESP_LOGI(droneTag, "Rotating Right");
    ESP_ERROR_CHECK(ledc_set_duty(LEDC_MODE, LEDC_CHANNEL_0, motorPower / 2));
    ESP_ERROR_CHECK(ledc_set_duty(LEDC_MODE, LEDC_CHANNEL_1, motorPower));
    ESP_ERROR_CHECK(ledc_set_duty(LEDC_MODE, LEDC_CHANNEL_2, motorPower));
    ESP_ERROR_CHECK(ledc_set_duty(LEDC_MODE, LEDC_CHANNEL_3, motorPower / 2));
    
    for (int i = 0; i < 4; i++) {
        ESP_ERROR_CHECK(ledc_update_duty(LEDC_MODE, led_channels[i]));
    }
}

void thrust() {
    lastActivityTime = esp_timer_get_time() / 1000;
    if (isSleeping) {
        return;
    }

    ESP_LOGI(droneTag, "Changing thrust");
    for (int i = 0; i < 4; i++) {
        ESP_ERROR_CHECK(ledc_set_duty(LEDC_MODE, led_channels[i], motorPower));
        ESP_ERROR_CHECK(ledc_update_duty(LEDC_MODE, led_channels[i]));
    }
}

void stopMovement() {
    ESP_LOGI(droneTag, "Stopping Movement");
    thrust();
}

void enterSleepMode() {
    ESP_LOGI(droneTag, "Entering sleep mode");
    isSleeping = true;
    
    // Turn off all motors
    for (int i = 0; i < 4; i++) {
        ESP_ERROR_CHECK(ledc_set_duty(LEDC_MODE, led_channels[i], 0));
        ESP_ERROR_CHECK(ledc_update_duty(LEDC_MODE, led_channels[i]));
    }
    
    // Disable MPU6050 to save power
    uint8_t data[2] = {0x6B, 0x40}; // PWR_MGMT_1 register
    i2c_master_write_to_device(I2C_MASTER_NUM, MPU6050_ADDR, data, sizeof(data), pdMS_TO_TICKS(1000));
}

void checkSleepCondition() {
    if (motorPower == 0 && !isSleeping) {
        uint64_t currentTime = esp_timer_get_time() / 1000; // Convert to milliseconds
        if (currentTime - lastActivityTime > sleepTimeout) {
            enterSleepMode();
        }
    }
}

void wakeupFromSleep() {
    ESP_LOGI(droneTag, "Waking from sleep mode");
    isSleeping = false;
    lastActivityTime = esp_timer_get_time() / 1000;
    
    // Wake up MPU6050
    uint8_t data[2] = {0x6B, 0x00};
    i2c_master_write_to_device(I2C_MASTER_NUM, MPU6050_ADDR, data, sizeof(data), pdMS_TO_TICKS(1000));
    setupMotors();
}

void setupWebServer() {
    server.on("/", HTTP_GET, [](AsyncWebServerRequest *request){
        String html = "<!DOCTYPE html><html><head><meta charset='UTF-8'><title>Drone Controller</title>";
        html += "<style>body { font-family: Arial, sans-serif; background-color: #1a1a1a; color: white; text-align: center; }";
        html += ".controller { display: grid; grid-template-columns: 1fr 2fr 1fr; gap: 50px; width: 600px; margin: auto; align-items: center; }";
        html += ".left-controls, .right-controls { display: flex; flex-direction: column; align-items: center; gap: 20px; }";
        html += ".middle-controls { display: grid; grid-template-columns: 60px 60px 60px; grid-template-rows: 60px 60px 60px; gap: 10px; justify-content: center; align-items: center; }";
        html += "button { background-color: #444; color: white; border: none; padding: 15px; font-size: 18px; border-radius: 8px; cursor: pointer; width: 60px; height: 60px; }";
        html += "button:hover { background-color: #4CAF50; } input[type=range] { writing-mode: vertical-lr; -webkit-appearance: slider-vertical; width: 20px; height: 200px; transform: rotate(180deg); }";
        html += ".sleep-notification { position: fixed; top: 20px; right: 20px; background-color: #ff5722; padding: 10px 20px; border-radius: 5px; display: ";
        html += isSleeping ? "block" : "none";
        html += "; }";
        html += "</style></head><body>";
        html += "<div class='sleep-notification' id='sleepNotification'>DRONE IS SLEEPING</div>";
        html += "<h1>Drone Controller</h1><div class='controller'>";
        html += "<div class='left-controls'><input type='range' min='0' max='255' value='" + String(motorPower) + "' id='motorPowerSlider' oninput='updateMotorPower()'><label>Motor Power: <span id='motorPowerValue'>" + String(motorPower) + "</span></label></div>";
        html += "<div class='middle-controls'><div></div> <button onclick='moveForward()'>&#9650;</button> <div></div>";
        html += "<button onclick='moveLeft()'>&#9664;</button> <div></div> <button onclick='moveRight()'>&#9654;</button>";
        html += "<div></div> <button onclick='moveBackward()'>&#9660;</button> <div></div></div>";
        html += "<div class='right-controls'><button onclick='rotateLeft()'>&#10226;</button><button onclick='rotateRight()'>&#10227;</button></div></div>";
        
        // Real time pitch/roll data
        html += "<h3>Realtime MPU Data</h3>";
        html += "<p>Pitch: <span id='pitchValue'>0.00</span>°</p>";
        html += "<p>Roll: <span id='rollValue'>0.00</span>°</p>";
    
        html += "<h3>Set PID Values</h3>";
        html += "<label>Kp: <input type='text' id='KpInput' value='" + String(Kp) + "'></label><br>";
        html += "<label>Ki: <input type='text' id='KiInput' value='" + String(Ki) + "'></label><br>";
        html += "<label>Kd: <input type='text' id='KdInput' value='" + String(Kd) + "'></label><br>";
        html += "<button onclick='sendPID()'>Update PID</button>";

        html += "<script>";
        html += "function checkSleepStatus() {";
        html += "  fetch('/getSleepStatus')";
        html += "    .then(response => response.json())";
        html += "    .then(data => {";
        html += "      const notification = document.getElementById('sleepNotification');";
        html += "      if (data.isSleeping) {";
        html += "        notification.style.display = 'block';";
        html += "      } else {";
        html += "        notification.style.display = 'none';";
        html += "      }";
        html += "    });";
        html += "}";
        html += "setInterval(checkSleepStatus, 1000);";
        html += "</script>";
    
        // Retrieve real time data
        html += "<script>";
        html += "function updateMotorPower() {";
        html += "    const power = document.getElementById('motorPowerSlider').value;";
        html += "    document.getElementById('motorPowerValue').innerText = power;";
        html += "    sendRequest(`/setMotorPower?value=${power}`);";
        html += "    document.getElementById('updateStatus').innerText = 'Motor Power wordt geüpdatet...';";
        html += "}";
        html += "function moveForward() { sendCommand('moveForward'); }";
        html += "function moveBackward() { sendCommand('moveBackward'); }";
        html += "function moveLeft() { sendCommand('moveLeft'); }";
        html += "function moveRight() { sendCommand('moveRight'); }";
        html += "function rotateLeft() { sendCommand('rotateLeft'); }";
        html += "function rotateRight() { sendCommand('rotateRight'); }";
        html += "function stopMovement() { sendCommand('stop'); }";
        html += "function sendCommand(command) { sendRequest(`/${command}`); }";
        html += "function sendRequest(url) { const xhr = new XMLHttpRequest(); xhr.open('GET', url, true); xhr.send(); }";
    
        // Update pitch and roll
        html += "function updateMPUData() {";
        html += "  fetch('/getMPUData')";
        html += "    .then(response => response.json())";
        html += "    .then(data => {";
        html += "      document.getElementById('pitchValue').innerText = data.pitch.toFixed(2);";
        html += "      document.getElementById('rollValue').innerText = data.roll.toFixed(2);";
        html += "    })";
        html += "    .catch(error => console.error('Error fetching MPU data:', error));";
        html += "}";
    
        html += "function sendPID() {";
        html += "  const Kp = document.getElementById('KpInput').value;";
        html += "  const Ki = document.getElementById('KiInput').value;";
        html += "  const Kd = document.getElementById('KdInput').value;";
        html += "  const url = `/setPID?Kp=${Kp}&Ki=${Ki}&Kd=${Kd}`;";
        html += "  fetch(url)";
        html += "    .then(response => response.text())";
        html += "    .then(data => {";
        html += "      console.log('PID Updated:', data);";
        html += "      alert('PID values updated successfully');";
        html += "    })";
        html += "    .catch(error => {";
        html += "      console.error('Error updating PID:', error);";
        html += "      alert('Failed to update PID values');";
        html += "    });";
        html += "};";
    
        // Update every 100ms
        html += "setInterval(updateMPUData, 100);";
        html += "</script></body></html>";
    
        request->send(200, "text/html", html);
    });

    // Return sleep status
    server.on("/getSleepStatus", HTTP_GET, [](AsyncWebServerRequest *request){
        String json = "{\"isSleeping\": ";
        json += isSleeping ? "true" : "false";
        json += "}";
        request->send(200, "application/json", json);
    });
    
    // Endpoint retrieving MPU data
    server.on("/getMPUData", HTTP_GET, [](AsyncWebServerRequest *request){
        String json = "{\"pitch\": ";
        json += String(pitch);
        json += ", \"roll\": ";
        json += String(roll);
        json += "}";
    
        request->send(200, "application/json", json);
    });
    
    // Endpoint for updating motorpower
    server.on("/setMotorPower", HTTP_GET, [](AsyncWebServerRequest *request){
        if (request->hasParam("value")) {
            String motorPowerStr = request->getParam("value")->value();
            int newPower = motorPowerStr.toInt();
            
            // Wake up when power changes
            if (isSleeping && newPower > 0) {
                wakeupFromSleep();
            }
            
            motorPower = newPower;
            lastActivityTime = esp_timer_get_time() / 1000;
            Serial.println("Motor Power Set to: " + String(motorPower));
            thrust();
    
            // Send confirmation with motor power, pitch, and roll 
            String responseMessage = "{\"status\": \"Motor power updated\", \"pitch\": ";
            responseMessage += String(pitch);
            responseMessage += ", \"roll\": ";
            responseMessage += String(roll);
            responseMessage += "}";
    
            request->send(200, "application/json", responseMessage);
        }
    });
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
extern "C" void app_main() {
    // Initialize watchdog
    initWatchdog();

    esp_timer_init();

    // Initialize nvs
    esp_err_t ret = nvs_flash_init();
    if (ret == ESP_ERR_NVS_NO_FREE_PAGES || ret == ESP_ERR_NVS_NEW_VERSION_FOUND) {
        ESP_ERROR_CHECK(nvs_flash_erase());
        ret = nvs_flash_init();
    }
    ESP_ERROR_CHECK(ret);

    // Initialize Arduino
    initArduino();
    
    Serial.begin(115200);

    // Drone control task
    xTaskCreate(
        droneControlTask,
        "DroneControl",
        4096,
        NULL,
        2,
        NULL
    );

    // WiFi task
    xTaskCreate(
        wifiTask,
        "WiFiTask",
        4096,
        NULL,
        1,
        NULL
    );

    // UDP emergency listener task
    xTaskCreate(
        udp_listener_task,
        "udp_listener",
        4096,
        NULL,
        2,
        &udpTaskHandle
    );

    // UDP telemetry broadcast task
    xTaskCreate(
        telemetryBroadcastTask,
        "Telemetry",
        4096,
        NULL,
        1,
        NULL
    );

    // Petting watchdog
    while (true) {
        petWatchdog();
        vTaskDelay(pdMS_TO_TICKS(100));
    }
}

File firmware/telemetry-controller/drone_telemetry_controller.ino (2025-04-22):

#include <Arduino.h>
#include <WiFi.h>
#include <WiFiUdp.h>
#include <Wire.h>
#include <LiquidCrystal_I2C.h>

#define BUTTON_PIN 18
LiquidCrystal_I2C lcd(0x27, 16, 2);

// Drone AP credentials
const char* ssid = "drone";
const char* password = "drone123";
WiFiUDP udp;

// Drone IP & UDP port
IPAddress droneIP(192, 168, 4, 1);
const int udpPort = 1234;

volatile bool emergencyTriggered = false;
unsigned long lastDebounceTime = 0;
const unsigned long debounceDelay = 200;

// Hardware interrupt
void IRAM_ATTR buttonISR() {
  if ((millis() - lastDebounceTime) > debounceDelay) {
    emergencyTriggered = true;
    lastDebounceTime = millis();
  }
}

void setup() {
  Serial.begin(115200);
  Wire.begin(21, 22);
  
  lcd.begin(16, 2);
  lcd.backlight();
  lcd.print("Initializing...");
  
  pinMode(BUTTON_PIN, INPUT_PULLUP);
  attachInterrupt(digitalPinToInterrupt(BUTTON_PIN), buttonISR, FALLING);
  
  // Connect to drone AP
  WiFi.begin(ssid, password);
  while (WiFi.status() != WL_CONNECTED) {
    delay(500);
    lcd.setCursor(0, 1);
    lcd.print("Connecting...");
  }
  
  lcd.clear();
  lcd.print("Connected!");
  lcd.setCursor(0, 1);
  lcd.print(WiFi.localIP());
  
  udp.begin(udpPort);
}

// Sending emergency packet to drone
void sendEmergencyPacket() {
  char message[] = "EMERGENCY_STOP";
  udp.beginPacket(droneIP, udpPort);
  udp.write((uint8_t*)message, sizeof(message));
  udp.endPacket();
}

void updateDisplay(float pitch, float roll) {
  char pitchBuffer[8];
  char rollBuffer[8];

  // Format pitch and roll
  snprintf(pitchBuffer, sizeof(pitchBuffer), "%+06.2f", pitch);
  snprintf(rollBuffer, sizeof(rollBuffer), "%+06.2f", roll);

  // Print pitch data
  lcd.clear();
  lcd.setCursor(0, 0);
  lcd.print("Pitch:");
  lcd.setCursor(9, 0);
  lcd.print(pitchBuffer);
  lcd.write(0xDF);

  // Print roll data
  lcd.setCursor(0, 1);
  lcd.print("Roll: ");
  lcd.setCursor(9, 1);
  lcd.print(rollBuffer);
  lcd.write(0xDF);
  delay(200);
}

void stopTriggerUpdate() {
  lcd.clear();
  lcd.print("Emergency Stop");
  lcd.setCursor(0, 1);
  lcd.print("Triggered!");
}

void loop() {
  if (emergencyTriggered) {
    lcd.setCursor(0, 0);
    sendEmergencyPacket();
    stopTriggerUpdate();
    
    while (digitalRead(BUTTON_PIN) == LOW) {
      delay(10);
    }
    
    emergencyTriggered = false;
  }
  
  // Check for telemetry data
  int packetSize = udp.parsePacket();
  if (packetSize) {
    char incomingPacket[50];
    int len = udp.read(incomingPacket, sizeof(incomingPacket));
    if (len > 0) {
      incomingPacket[len] = '\0';
      
      // Parse telemetry data
      char* pitchStr = strstr(incomingPacket, "PITCH:");
      char* rollStr = strstr(incomingPacket, "ROLL:");
      
      // Extract data and convert to float
      if (pitchStr && rollStr) {
        float pitch = atof(pitchStr + 6);
        float roll = atof(rollStr + 5);
        updateDisplay(pitch, roll);
      }
    }
  }
  
  delay(10);
}

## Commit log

2025-03-19 Created circuit diagram
    [embedded-systems-drone.kicad_sch]
2025-04-21 Updated drone schematic. Moved designs folder into docs.
    [embedded-systems-drone.kicad_sch]
2025-04-21 Added telemetry controller schematic
    [embedded-systems-telemetry-controller.kicad_sch]
2025-04-22 Saved schematics to PDFs
2025-04-22 Added drone 3D model. Moved schematics to own folder.
    [Drone.stl, embedded-systems-drone.kicad_sch, embedded-systems-telemetry-controller.kicad_sch]
2025-06-29 Added descriptive document and necessary docs
    [Batteryholder.stl, Drone.stl, micro105-bottom-v2.stl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]
